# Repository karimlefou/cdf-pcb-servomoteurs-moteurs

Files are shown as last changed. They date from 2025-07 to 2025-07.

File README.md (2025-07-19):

                    pcb servomoteurs et moteurs 
ce pcb est déduie a la coupe de france de robotique de 2026 , il permet de controle les moteurs et specialement les servomoteurs en deux façon : uart et pwm 
et aussi c'est un 4 couche , avec la couche power qui coupe en 3 .
schématique : 



stm 32 et ses complements : 



et les régulateurs :



et on a precise les empreintes : 





et pour le routage je suis finis de poser mes composants et je vais commencer a relier :



et la couche GND : 


la couche haute  rouge:


et la couche basse bleu :

et la couche power :


pour l'epaisseur des fils et vias  , je me suis base sur cette formule 



merci a @CaptainJaja pour les contributions 


voila si vous avez des remarques je suis preneur .

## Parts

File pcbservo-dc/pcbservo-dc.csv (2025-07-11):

Reference | Qty | Value | DNP | Exclude from BOM | Exclude from Board | Footprint | Datasheet
C1,C2 | 2 | 1uF |  |  |  | Capacitor_SMD:C_0603_1608Metric_Pad1.08x0.95mm_HandSolder | ~
C3,C5,C8,C9,C10,C12,C19,C25 | 8 | 100n |  |  |  | Capacitor_SMD:C_0402_1005Metric | ~
C4,C6 | 2 | 10u |  |  |  | Capacitor_SMD:C_0805_2012Metric | ~
C7 | 1 | 4u7 |  |  |  | Capacitor_SMD:C_0805_2012Metric | ~
C11,C13 | 2 | 10n |  |  |  | Capacitor_SMD:C_0402_1005Metric | ~
C14 | 1 | 1u |  |  |  | Capacitor_SMD:C_0402_1005Metric | ~
C15 | 1 | 10u |  |  |  | Capacitor_SMD:C_0603_1608Metric | ~
C16 | 1 | 100n |  |  |  | Capacitor_SMD:C_0603_1608Metric | ~
C17 | 1 | 150p |  |  |  | Capacitor_SMD:C_0603_1608Metric | ~
C18 | 1 | 22u |  |  |  | Capacitor_SMD:C_0805_2012Metric | ~
C20,C22,C24 | 3 | 47µ |  |  |  | Capacitor_SMD:CP_Elec_6.3x5.7 | ~
C21,C23,C28,C29,C30 | 5 | 0.1µ |  |  |  | Capacitor_SMD:C_0603_1608Metric | ~
C26,C27 | 2 | 2u2 |  |  |  | Capacitor_SMD:C_0805_2012Metric | ~
C32,C33 | 2 | 20p |  |  |  | Capacitor_SMD:C_0603_1608Metric | ~
D1 | 1 | 1N5822 |  |  |  | Diode_SMD:D_SMB | http://www.vishay.com/docs/88526/1n5820.pdf
D2,D3,D4 | 3 | 1N5819 |  |  |  | Diode_THT:D_DO-41_SOD81_P10.16mm_Horizontal | http://www.vishay.com/docs/88525/1n5817.pdf
Driver1 | 1 | TB6612FNG |  |  |  | Package_SO:SSOP-24_5.3x8.2mm_P0.65mm | https://toshiba.semicon-storage.com/us/product/linear/motordriver/detail.TB6612FNG.html
H1,H2,H3,H4 | 4 | MountingHole_Pad |  | Exclure de la Liste du Matériel |  | MountingHole:MountingHole_2.7mm_M2.5_Pad | ~
IC1,IC2,IC3 | 3 | NC7WZ241K8X |  |  |  | NC7WZ241K8X:UQFN8 1.6X1.6, 0.5P | https://www.onsemi.com/pub/Collateral/NC7WZ241-D.PDF
J1,J2 | 2 | Conn_01x02 |  |  |  | Connector_JST:JST_XH_S2B-XH-A-1_1x02_P2.50mm_Horizontal | ~
J3 | 1 | BU33SD5WG-TR |  |  |  | Package_TO_SOT_SMD:SOT-23-5
J4,J5,J10 | 3 | Conn_01x03 |  |  |  | Connector_JST:JST_XH_B3B-XH-A_1x03_P2.50mm_Vertical | ~
J7 | 1 | Conn_ST_STDC14 |  |  |  | Connector_PinHeader_1.27mm:PinHeader_2x07_P1.27mm_Vertical_SMD | https://www.st.com/content/ccc/resource/technical/document/user_manual/group1/99/49/91/b6/b2/3a/46/e5/DM00526767/files/DM00526767.pdf/jcr:content/translations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
J8 | 1 | Conn_01x03 |  |  |  | Connector_JST:JST_PH_B3B-PH-K_1x03_P2.00mm_Vertical | ~
J12,J13 | 2 | Conn_01x02 |  |  |  | Connector_JST:JST_XH_B2B-XH-A_1x02_P2.50mm_Vertical | ~
J14 | 1 | R-78B5.0-2.0 |  |  |  | Converter_DCDC:Converter_DCDC_RECOM_R-78B-2.0_THT | https://www.recom-power.com/pdf/Innoline/R-78Bxx-2.0.pdf
L1 | 1 | 39n |  |  |  | Inductor_SMD:L_0603_1608Metric | ~
L2 | 1 | 15u |  |  |  | Inductor_SMD:L_12x12mm_H4.5mm | ~
R1,R2,R3,R4,R5,R6,R13,R18,R19 | 9 | 10k |  |  |  | Resistor_SMD:R_0402_1005Metric | ~
R7 | 1 | 24.9k |  |  |  | Resistor_SMD:R_0603_1608Metric | ~
R8,R9,R10 | 3 | 100k |  |  |  | Resistor_SMD:R_0603_1608Metric | ~
R11 | 1 | 261k |  |  |  | Resistor_SMD:R_0603_1608Metric | ~
R12 | 1 | 40.2k |  |  |  | Resistor_SMD:R_0603_1608Metric | ~
R15,R16 | 2 | 220 |  |  |  | Resistor_SMD:R_0402_1005Metric | ~
SW1,SW2,SW3,SW4,SW5,SW6 | 6 | SW_Nidec_CAS-120A1 |  |  |  | Button_Switch_SMD:Nidec_Copal_CAS-120A | https://www.nidec-components.com/e/catalog/switch/cas.pdf
Switch1 | 1 | 430471025826 |  |  |  | Button_Switch_THT:SW_PUSH_6mm
TP1,TP2 | 2 | TestPoint |  |  |  | TestPoint:TestPoint_Pad_D2.0mm | ~
U2 | 1 | ~ |  |  |  | Package_SO:SOIC-8_3.9x4.9mm_P1.27mm | kicad-embed://MP1584.PDF
U7 | 1 | STM32H573RITx |  |  |  | Package_QFP:LQFP-64_10x10mm_P0.5mm | https://www.st.com/resource/en/datasheet/stm32h573ri.pdf
U17 | 1 | ~ |  |  |  | Crystal:Crystal_SMD_3225-4Pin_3.2x2.5mm | https://www.we-online.com/components/products/datasheet/830026380.pdf

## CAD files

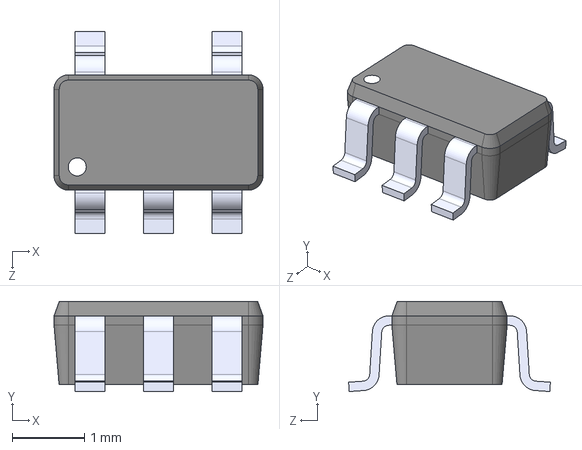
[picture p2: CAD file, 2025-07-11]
pcbservo-dc/BU33SD5WG-TR/BU33SD5WG-TR.step
2.90 x 1.25 x 2.80 mm

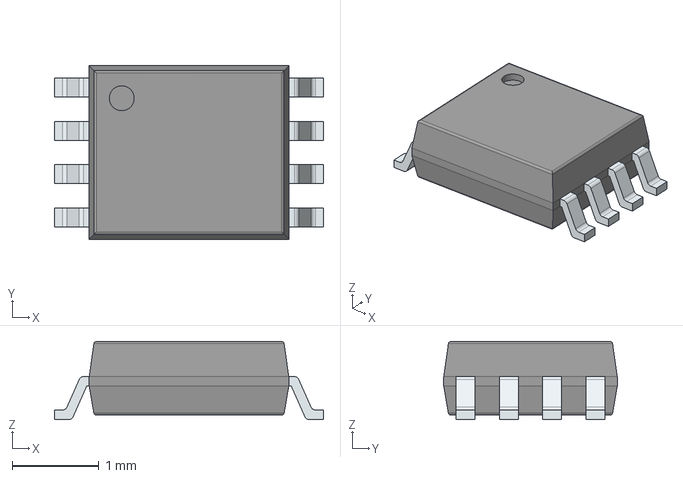
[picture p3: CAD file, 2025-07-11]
pcbservo-dc/NC7WZ241K8X/3D/NC7WZ241K8X.stp
3.10 x 2.00 x 0.9 mm
PinsArrayLR

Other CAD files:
pcbservo-dc/MPQ4317GRE-5-AEC1-Z/Allegro/mpq4317gre5aec1z.psm
pcbservo-dc/MPQ4317GRE-5-AEC1-Z/DEHDL/mpq4317gre_5_aec1_z/chips/chips.prt
pcbservo-dc/NC7WZ241K8X/Allegro/sop50p310x90-8n.psm
pcbservo-dc/NC7WZ241K8X/DEHDL/nc7wz241k8x/chips/chips.prt

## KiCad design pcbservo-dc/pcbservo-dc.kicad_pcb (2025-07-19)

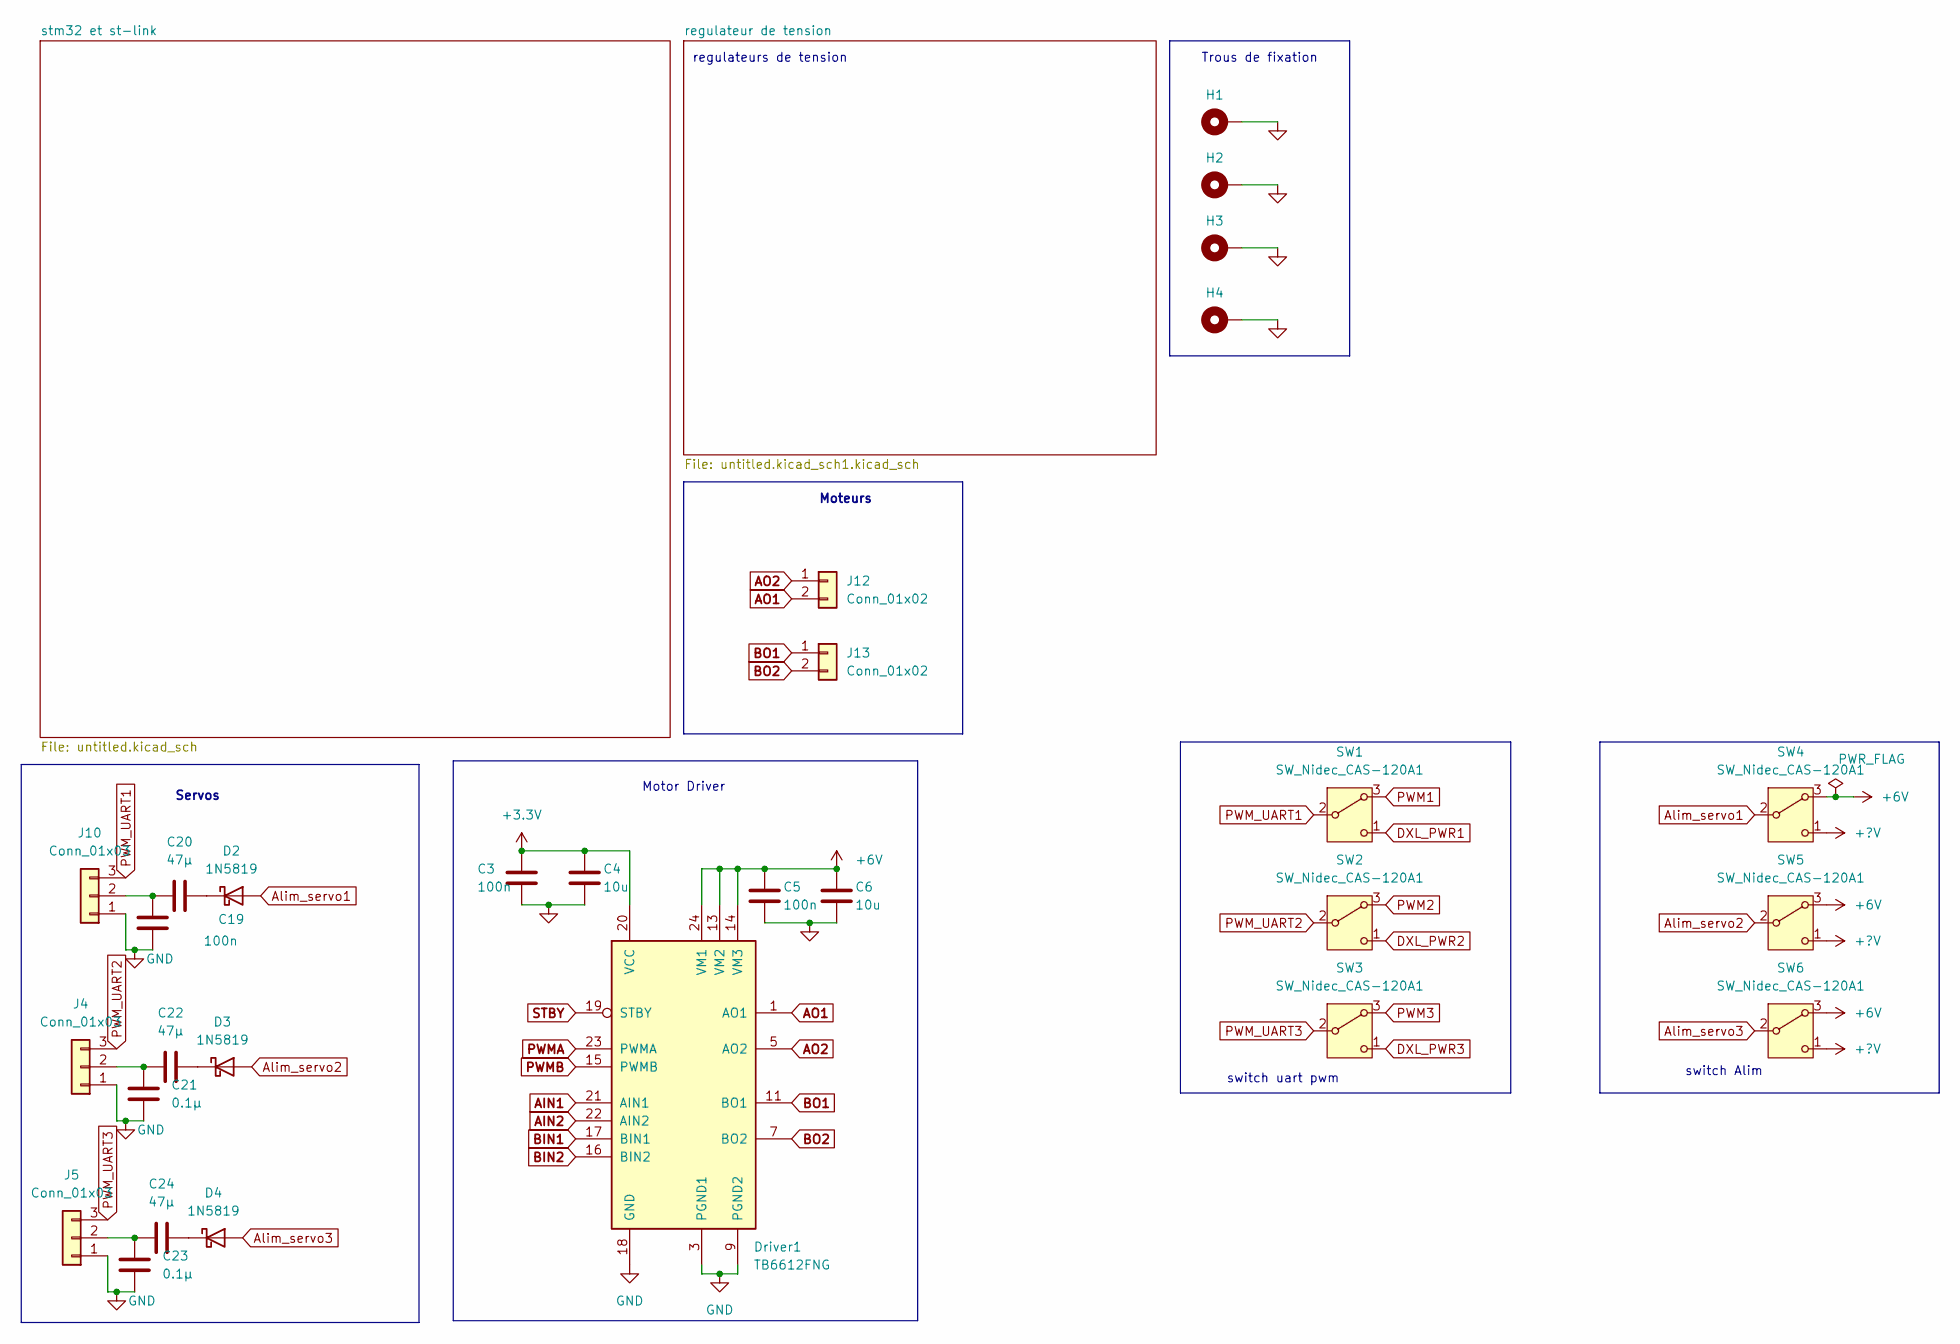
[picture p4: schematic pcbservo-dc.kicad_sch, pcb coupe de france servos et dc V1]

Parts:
C3, C5: 100n; C_0402_1005Metric
C4, C6: 10u; C_0805_2012Metric
C19: 100n; C_0603_1608Metric
C20, C22, C24: 47µ; CP_Elec_6.3x5.7
C21, C23: 0.1µ; C_0603_1608Metric
D2, D3, D4: 1N5819; D_DO-41_SOD81_P10.16mm_Horizontal
Driver1: TB6612FNG; SSOP-24_5.3x8.2mm_P0.65mm
H1, H2, H3, H4: MountingHole_Pad; MountingHole_2.7mm_M2.5_Pad
J4, J5, J10: Conn_01x03; JST_XH_B3B-XH-A_1x03_P2.50mm_Vertical
J12, J13: Conn_01x02; JST_XH_B2B-XH-A_1x02_P2.50mm_Vertical
SW1, SW2, SW3, SW4, SW5, SW6: SW_Nidec_CAS-120A1; Nidec_Copal_CAS-120A

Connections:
+3.3V: C3.1, C4.1, Driver1.20 (VCC); also elsewhere on the board
+6V: C5.1, C6.1, Driver1.13 (VM2), Driver1.14 (VM3), Driver1.24 (VM1), SW4.3 (A), SW5.3 (A), SW6.3 (A); also elsewhere on the board
+?V: SW4.1 (C), SW5.1 (C), SW6.1 (C); also elsewhere on the board
AIN1: Driver1.21 (AIN1); also elsewhere on the board
AIN2: Driver1.22 (AIN2); also elsewhere on the board
AO1: Driver1.1 (AO1), Driver1.2 (AO1), J12.2
AO2: Driver1.5 (AO2), Driver1.6 (AO2), J12.1
Alim_servo1: D2.2 (A), SW4.2 (B)
Alim_servo2: D3.2 (A), SW5.2 (B)
Alim_servo3: D4.2 (A), SW6.2 (B)
BIN1: Driver1.17 (BIN1); also elsewhere on the board
BIN2: Driver1.16 (BIN2); also elsewhere on the board
BO1: Driver1.11 (BO1), Driver1.12 (BO1), J13.1
BO2: Driver1.7 (BO2), Driver1.8 (BO2), J13.2
DXL_PWR1: SW1.1 (C); also elsewhere on the board
DXL_PWR2: SW2.1 (C); also elsewhere on the board
DXL_PWR3: SW3.1 (C); also elsewhere on the board
GND: C3.2, C4.2, C5.2, C6.2, C19.2, C21.2, C23.2, Driver1.3 (PGND1), Driver1.4 (PGND1), Driver1.9 (PGND2), Driver1.10 (PGND2), Driver1.18 (GND), H1.1, H2.1, H3.1, H4.1, J4.1, J5.1, J10.1; also elsewhere on the board
unnamed: C20.2, D2.1 (K)
unnamed: C22.2, D3.1 (K)
unnamed: C24.2, D4.1 (K)
unnamed: C21.1, C22.1, J4.2
unnamed: C23.1, C24.1, J5.2
unnamed: C19.1, C20.1, J10.2
PWM1: SW1.3 (A); also elsewhere on the board
PWM2: SW2.3 (A); also elsewhere on the board
PWM3: SW3.3 (A); also elsewhere on the board
PWMA: Driver1.23 (PWMA); also elsewhere on the board
PWMB: Driver1.15 (PWMB); also elsewhere on the board
PWM_UART1: J10.3, SW1.2 (B)
PWM_UART2: J4.3, SW2.2 (B)
PWM_UART3: J5.3, SW3.2 (B)
STBY: Driver1.19 (STBY); also elsewhere on the board

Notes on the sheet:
Trous de fixation
switch uart pwm
Servos
switch Alim
regulateurs de tension
Moteurs
Motor Driver

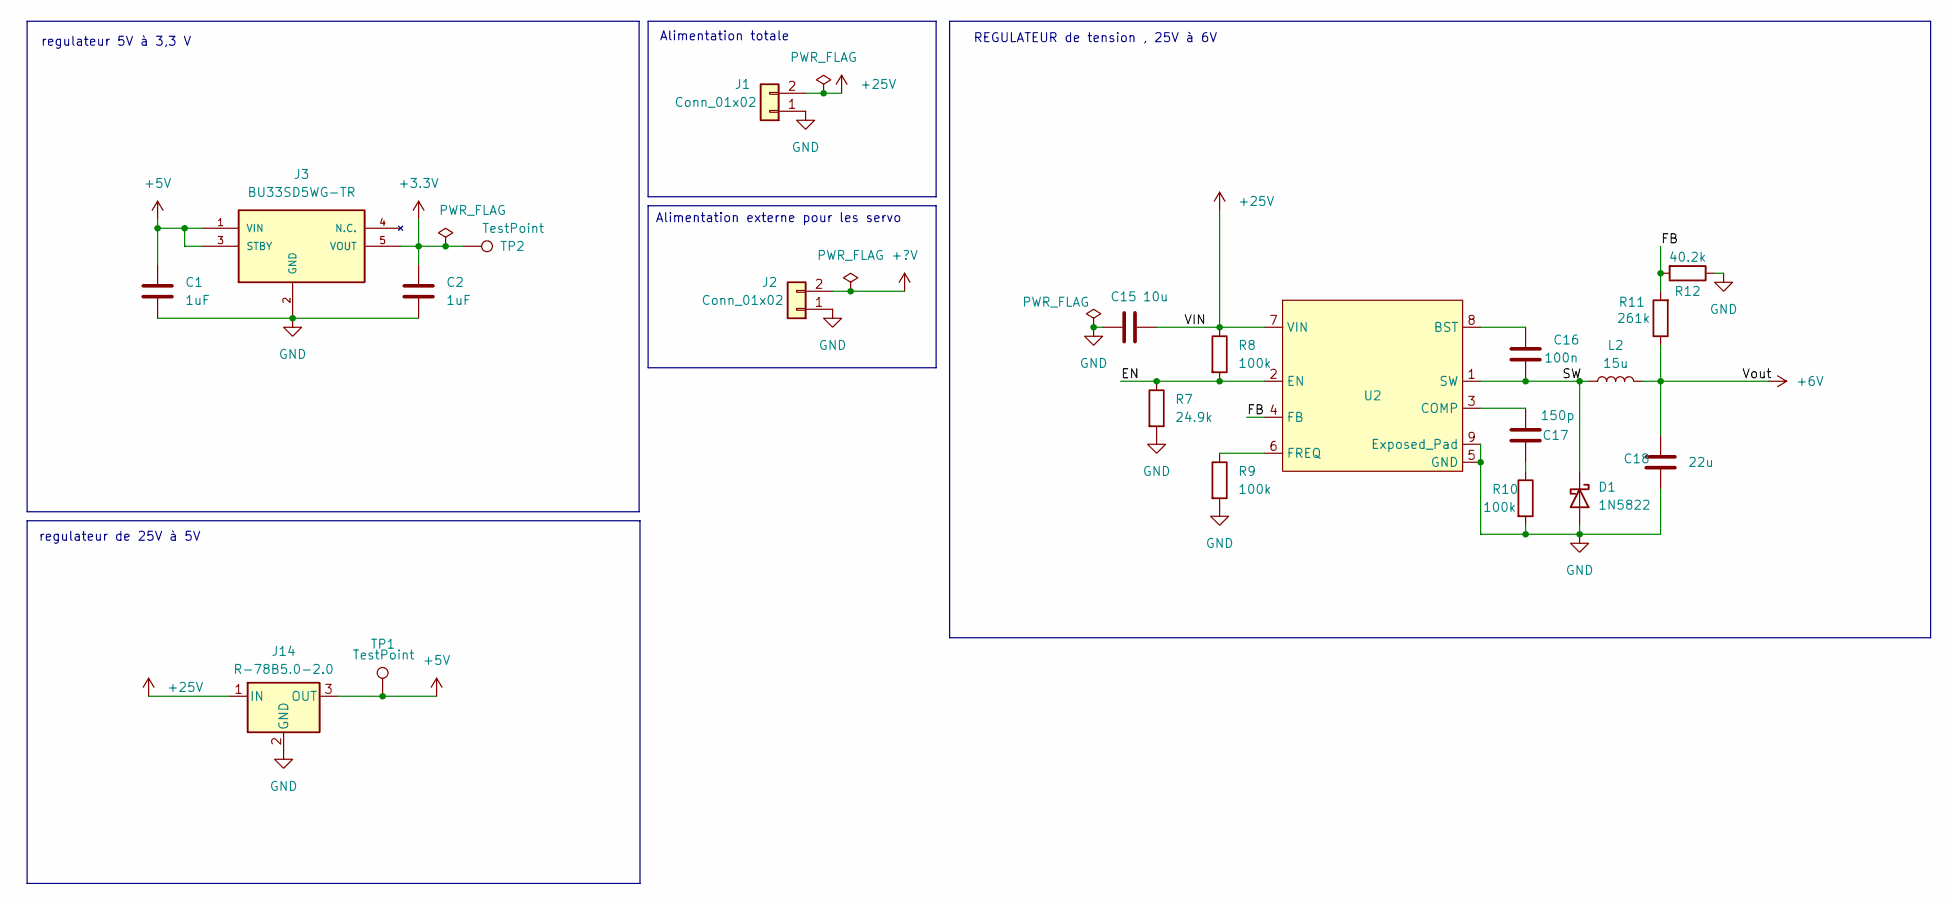
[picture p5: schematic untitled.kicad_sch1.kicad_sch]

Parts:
C1, C2: 1uF; C_0603_1608Metric_Pad1.08x0.95mm_HandSolder
C15: 10u; C_0603_1608Metric
C16: 100n; C_0603_1608Metric
C17: 150p; C_0603_1608Metric
C18: 22u; C_0805_2012Metric
D1: 1N5822; D_SMB
J1, J2: Conn_01x02; JST_XH_B2B-XH-A_1x02_P2.50mm_Vertical
J3: BU33SD5WG-TR; SOT-23-5; Mouser_Part_Number 755-BU33SD5WG-TR
J14: R-78B5.0-2.0; Converter_DCDC_RECOM_R-78B-2.0_THT
L2: 15u; L_12x12mm_H4.5mm
R7: 24.9k; R_0603_1608Metric
R8, R9, R10: 100k; R_0603_1608Metric
R11: 261k; R_0603_1608Metric
R12: 40.2k; R_0603_1608Metric
TP1, TP2: TestPoint; TestPoint_Pad_D1.0mm
U2: MP1584-SOICP8

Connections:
+3.3V: C2.1, J3.5 (VOUT), TP2.1; also elsewhere on the board
+5V: C1.1, J3.1 (VIN), J3.3 (STBY), J14.3 (OUT), TP1.1; also elsewhere on the board
+6V: C18.1, L2.2, R11.1; also elsewhere on the board
+25V: C15.1, J1.2, J14.1 (IN), R8.1, U2.7 (VIN)
+?V: J2.2; also elsewhere on the board
/regulateur de tension/EN: R7.1, R8.2, U2.2 (EN)
/regulateur de tension/FB: R11.2, R12.2, U2.4 (FB)
/regulateur de tension/SW: C16.2, D1.1 (K), L2.1, U2.1 (SW)
GND: C1.2, C2.2, C15.2, C18.2, D1.2 (A), J1.1, J2.1, J3.2 (GND), J14.2 (GND), R7.2, R9.2, R10.2, R12.1, U2.5 (GND), U2.9 (Exposed_Pad); also elsewhere on the board
unnamed: C17.2, R10.1
unnamed: C16.1, U2.8 (BST)
unnamed: C17.1, U2.3 (COMP)
unnamed: R9.1, U2.6 (FREQ)

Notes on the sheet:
regulateur 5V à 3,3 V
Alimentation externe pour les servo
REGULATEUR de tension , 25V à 6V
regulateur de 25V à 5V
Alimentation totale

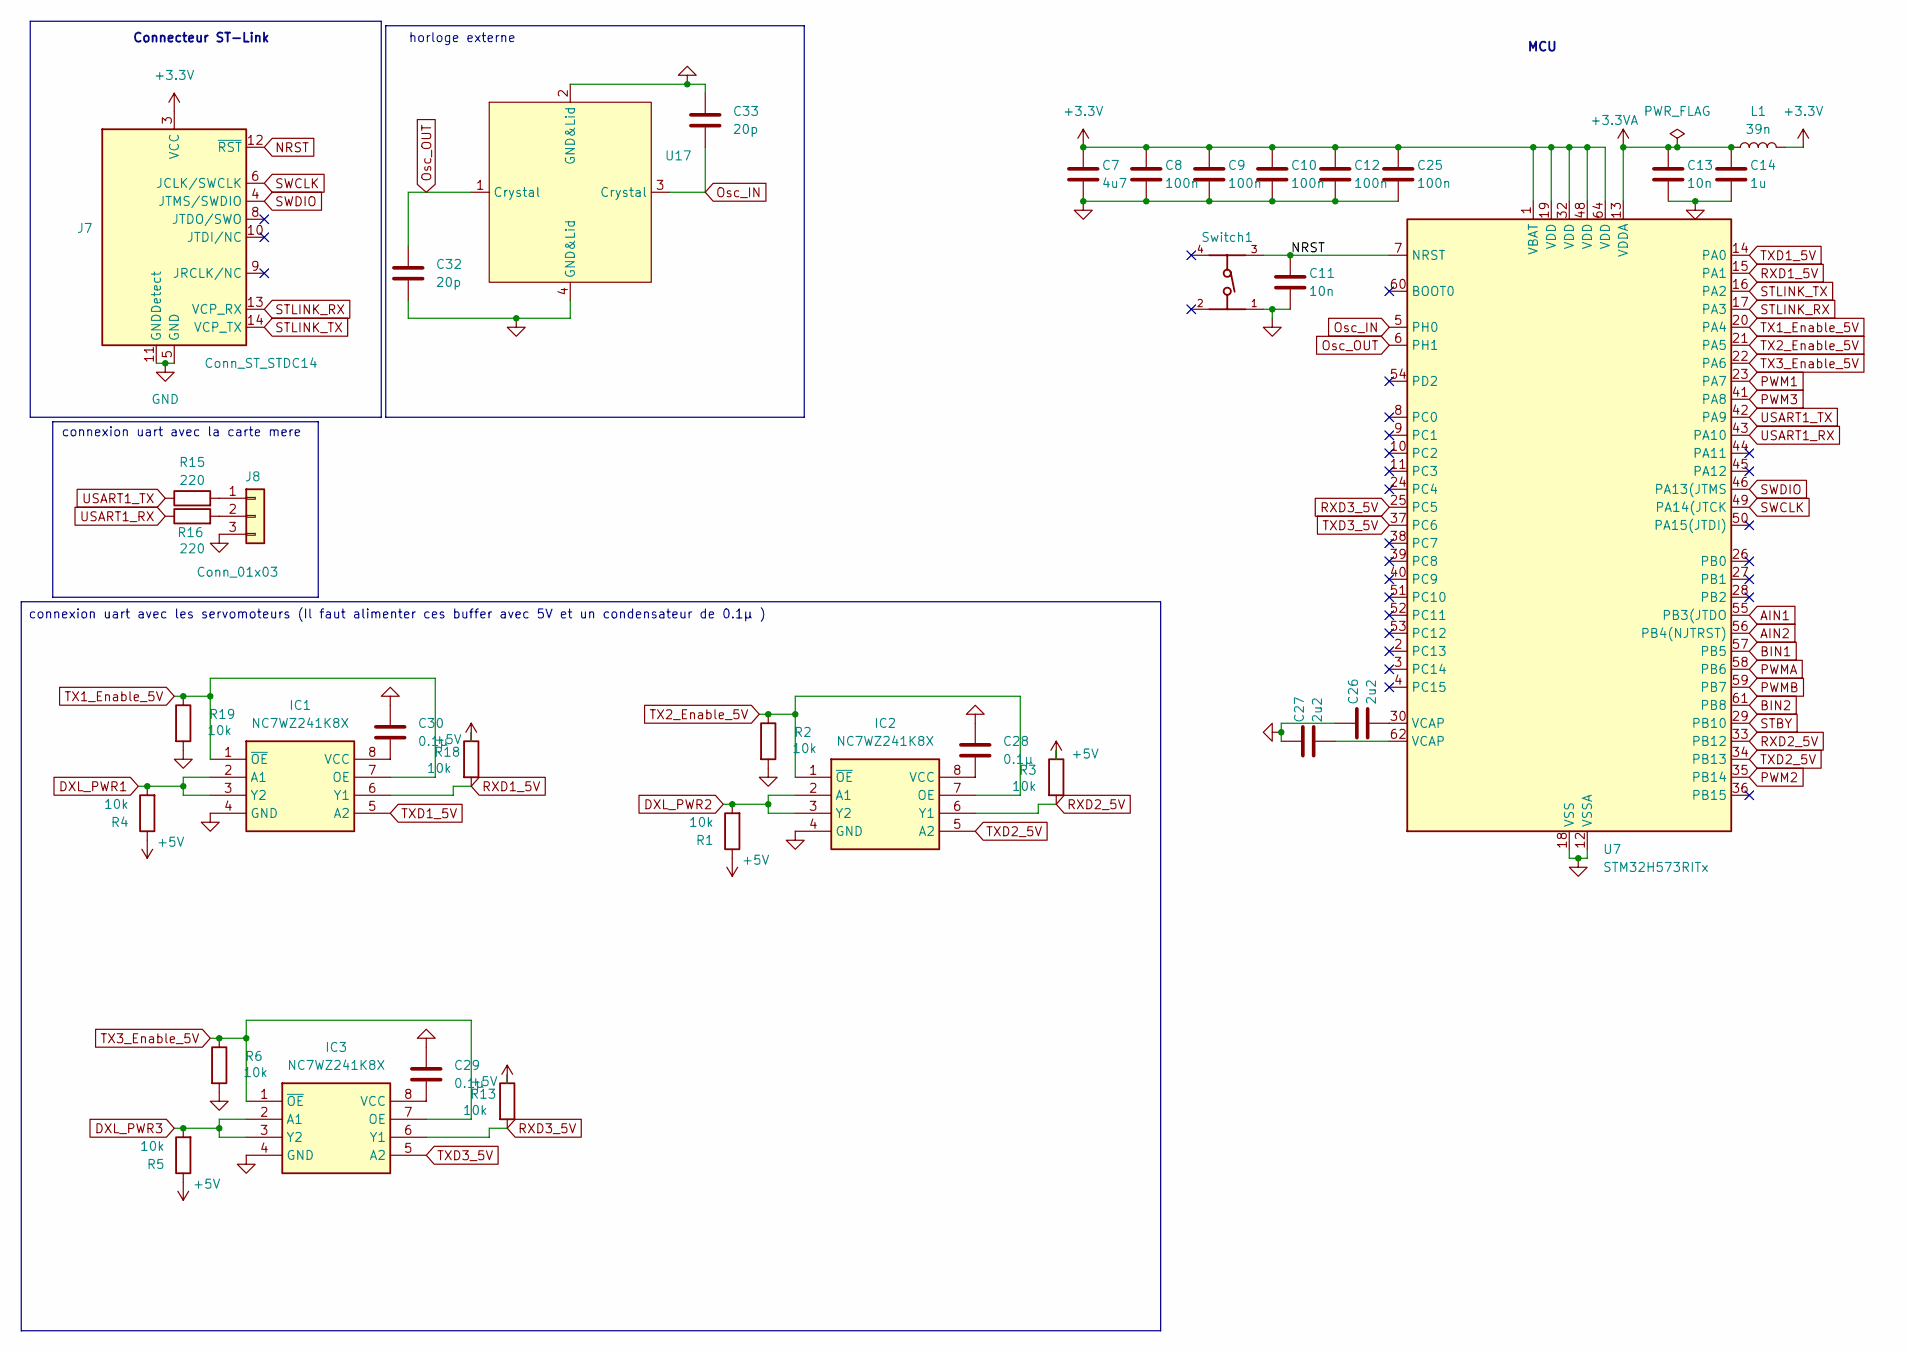
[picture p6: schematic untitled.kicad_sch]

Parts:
C7: 4u7; C_0805_2012Metric
C8, C9, C10, C12, C25: 100n; C_0402_1005Metric
C11, C13: 10n; C_0402_1005Metric
C14: 1u; C_0402_1005Metric
C26, C27: 2u2; C_0805_2012Metric
C28, C29, C30: 0.1µ; C_0603_1608Metric
C32, C33: 20p; C_0603_1608Metric
IC1, IC2, IC3: NC7WZ241K8X; UQFN8 1.6X1.6, 0.5P; Mouser Part Number 512-NC7WZ241K8X
J7: Conn_ST_STDC14; PinHeader_2x07_P1.27mm_Vertical_SMD
J8: Conn_01x03; JST_PH_B3B-PH-K_1x03_P2.00mm_Vertical
L1: 39n; L_0603_1608Metric
R1, R2, R3, R4, R5, R6, R13, R18, R19: 10k; R_0402_1005Metric
R15, R16: 220; R_0402_1005Metric
Switch1: 430471025826; BOUTONPOUSSOIR; PART-NUMBER 430471025826
U7: STM32H573RITx; LQFP-64_10x10mm_P0.5mm
U17: Crystal_SMD_3225-4Pin_3.2x2.5mm

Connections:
+3.3V: C7.1, C8.1, C9.1, C10.1, C12.1, C25.1, J7.3 (VCC), L1.2, U7.1 (VBAT), U7.19 (VDD), U7.32 (VDD), U7.48 (VDD), U7.64 (VDD); also elsewhere on the board
+3.3VA: C13.1, C14.1, L1.1, U7.13 (VDDA)
+5V: R1.1, R3.1, R4.1, R5.1, R13.1, R18.1; also elsewhere on the board
AIN1: U7.55 (PB3(JTDO); also elsewhere on the board
AIN2: U7.56 (PB4(NJTRST)); also elsewhere on the board
BIN1: U7.57 (PB5); also elsewhere on the board
BIN2: U7.61 (PB8); also elsewhere on the board
DXL_PWR1: IC1.2 (A1), IC1.3 (Y2), R4.2; also elsewhere on the board
DXL_PWR2: IC2.2 (A1), IC2.3 (Y2), R1.2; also elsewhere on the board
DXL_PWR3: IC3.2 (A1), IC3.3 (Y2), R5.2; also elsewhere on the board
GND: C7.2, C8.2, C9.2, C10.2, C11.2, C12.2, C13.2, C14.2, C25.2, C26.1, C27.1, C28.1, C29.1, C30.1, C32.2, C33.1, IC1.4 (GND), IC2.4 (GND), IC3.4 (GND), J7.5 (GND), J7.7 (GND), J7.11 (GNDDetect), J8.3, R2.2, R6.2, R19.2, Switch1.1, U7.12 (VSSA), U7.18 (VSS), U7.31 (VSS), U7.47 (VSS), U7.63 (VSS), U17.2 (GND&Lid), U17.4 (GND&Lid); also elsewhere on the board
NRST: C11.1, J7.12 (~RST), Switch1.3, U7.7 (NRST)
unnamed: C26.2, U7.30 (VCAP)
unnamed: C27.2, U7.62 (VCAP)
unnamed: C30.2, IC1.8 (VCC)
unnamed: C28.2, IC2.8 (VCC)
unnamed: C29.2, IC3.8 (VCC)
unnamed: J8.1, R15.2
unnamed: J8.2, R16.2
Osc_IN: C33.2, U7.5 (PH0), U17.3 (Crystal)
Osc_OUT: C32.1, U7.6 (PH1), U17.1 (Crystal)
PWM1: U7.23 (PA7); also elsewhere on the board
PWM2: U7.35 (PB14); also elsewhere on the board
PWM3: U7.41 (PA8); also elsewhere on the board
PWMA: U7.58 (PB6); also elsewhere on the board
PWMB: U7.59 (PB7); also elsewhere on the board
RXD1_5V: IC1.6 (Y1), R18.2, U7.15 (PA1)
RXD2_5V: IC2.6 (Y1), R3.2, U7.33 (PB12)
RXD3_5V: IC3.6 (Y1), R13.2, U7.25 (PC5)
STBY: U7.29 (PB10); also elsewhere on the board
STLINK_RX: J7.13 (VCP_RX), U7.17 (PA3)
STLINK_TX: J7.14 (VCP_TX), U7.16 (PA2)
SWCLK: J7.6 (JCLK/SWCLK), U7.49 (PA14(JTCK)
SWDIO: J7.4 (JTMS/SWDIO), U7.46 (PA13(JTMS)
TX1_Enable_5V: IC1.1 (~OE), IC1.7 (OE), R19.1, U7.20 (PA4)
TX2_Enable_5V: IC2.1 (~OE), IC2.7 (OE), R2.1, U7.21 (PA5)
TX3_Enable_5V: IC3.1 (~OE), IC3.7 (OE), R6.1, U7.22 (PA6)
TXD1_5V: IC1.5 (A2), U7.14 (PA0)
TXD2_5V: IC2.5 (A2), U7.34 (PB13)
TXD3_5V: IC3.5 (A2), U7.37 (PC6)
USART1_RX: R16.1, U7.43 (PA10)
USART1_TX: R15.1, U7.42 (PA9)

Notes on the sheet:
connexion uart avec la carte mere
horloge externe
Connecteur ST-Link
MCU
connexion uart avec les servomoteurs (Il faut alimenter ces buffer avec 5V et un condensateur de 0.1µ )

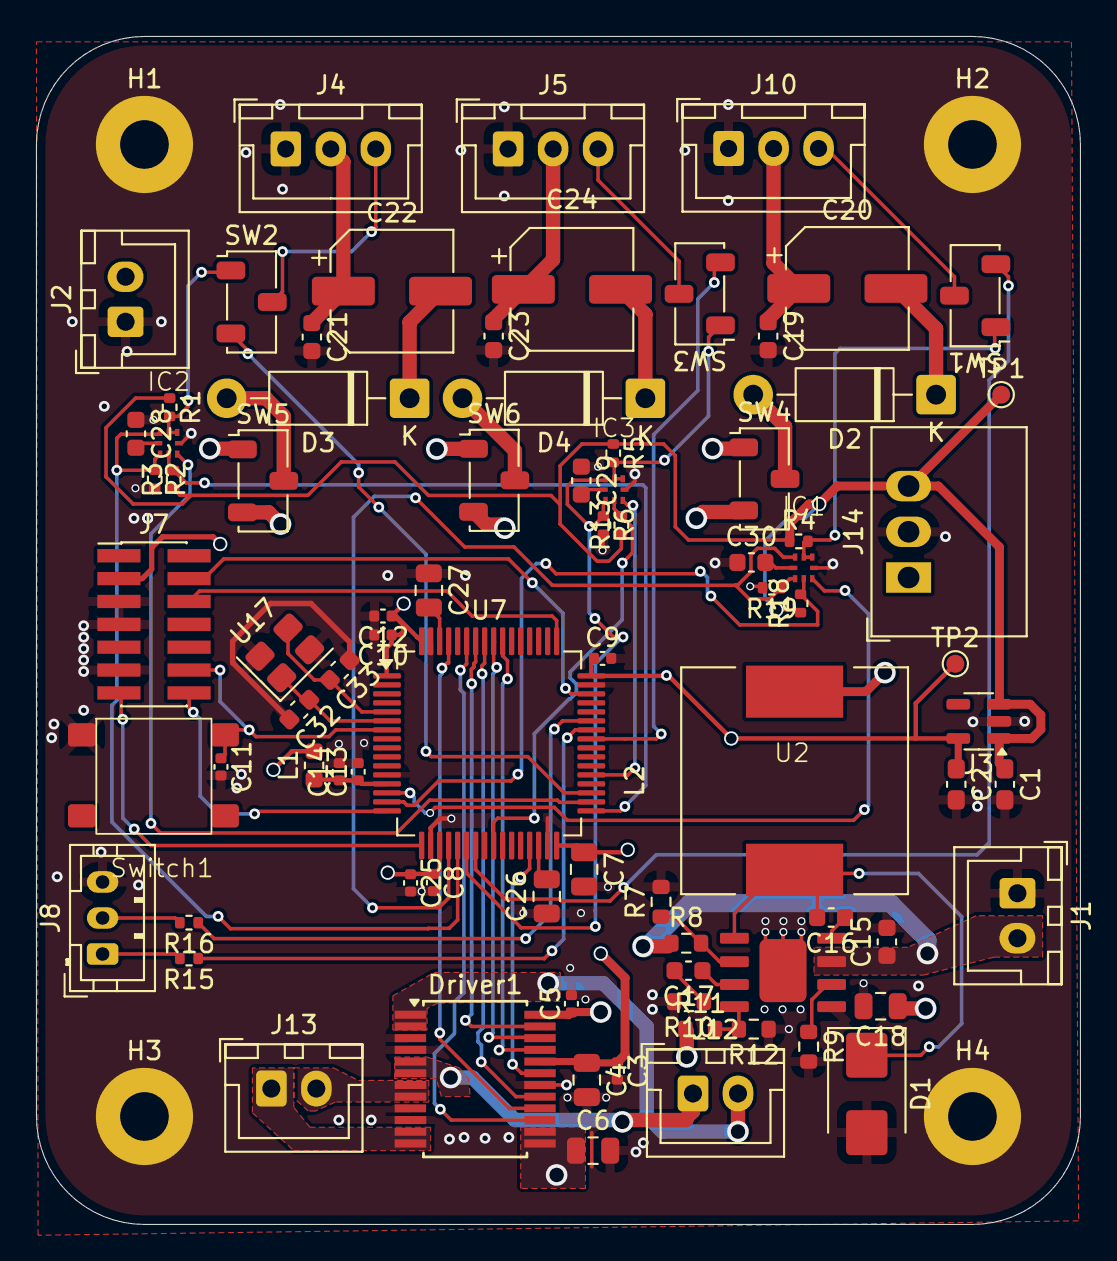
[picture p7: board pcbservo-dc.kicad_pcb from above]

Board: 4 copper layers, 58.0 x 66.0 mm, 86 parts (0 on the bottom side), 68 nets.

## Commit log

2025-07-11 Intial commit
    [BU33SD5WG-TR.step, EDI2CAP.CFG, MPQ4317GRE-5-AEC1-Z.stp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]
2025-07-12 en train de router
    [pcbservo-dc.kicad_pcb]
2025-07-12 le retouage est bientot fini , il reste que les petit signaus rx tx et configuere l horloge externe et power
    [pcbservo-dc.kicad_pcb]
2025-07-14 fin de routage mais correction des erreur
    [pcbservo-dc.kicad_pcb]
2025-07-17 résolution des erreurs
    [pcbservo-dc.kicad_pcb, pcbservo-dc.kicad_sch, untitled.kicad_sch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]
2025-07-19 version finale
    [pcbservo-dc.kicad_pcb]
